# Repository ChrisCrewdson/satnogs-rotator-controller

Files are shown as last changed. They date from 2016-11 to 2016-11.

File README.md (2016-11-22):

# SatNOGS Rotator Controller

Firmware and electronics designs for [SatNOGS Rotator](https://github.com/satnogs/satnogs-rotator/).

Repository includes all source files for PCB's and firmware for the SatNOGS rotator controller assembly.

## Documentation

More information can be found in our [documentation](http://satnogs.org/documentation/hardware/), or our [wiki](https://wiki.satnogs.org).

Please check the documentation to find which release of the rotator controller matches your mechanical rotator version.

## Repository policy
SatNOGS hardware repositories only track source design files. All needed derivative files (e.g. stl, grb etc) for production are created per release, packaged in an archive and uploaded linked to a  [release](https://github.com/satnogs/satnogs-rotator-controller/releases).

Each major release (x.0.0) is branched out of master. Subsequent fixes (minor or not) are commited on those branches and tagged accordingly.

Master branch is most times under active development, so expect things to break. For production ready and previous releases source files check tags and branches.

## License

&copy; 2014-2015 [Libre Space Foundation](http://librespacefoundation.org).

Licensed under the [CERN OHLv1.2](LICENSE).

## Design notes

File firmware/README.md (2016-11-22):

Arduino Code
============

In order to use this code, you need to put the AccelStepper v1.46 library and SoftI2CMaster library in your libraries folder. Thanks to [AccelStepper library](http://www.airspayce.com/mikem/arduino/AccelStepper/) and [SoftI2CMaster](https://github.com/todbot/SoftI2CMaster).

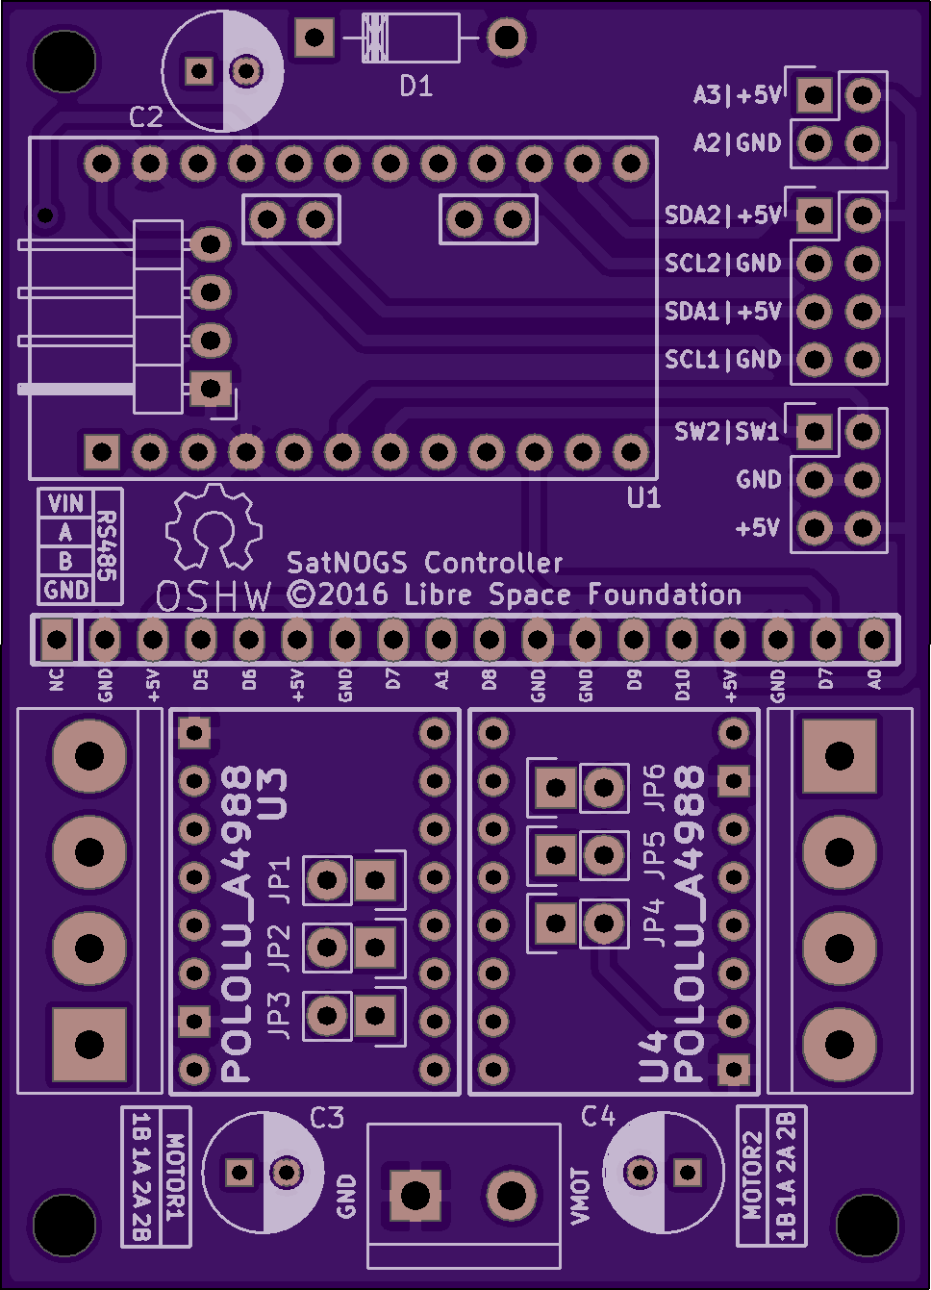
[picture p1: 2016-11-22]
PCB/satnogs_controller/oshpark_top.png

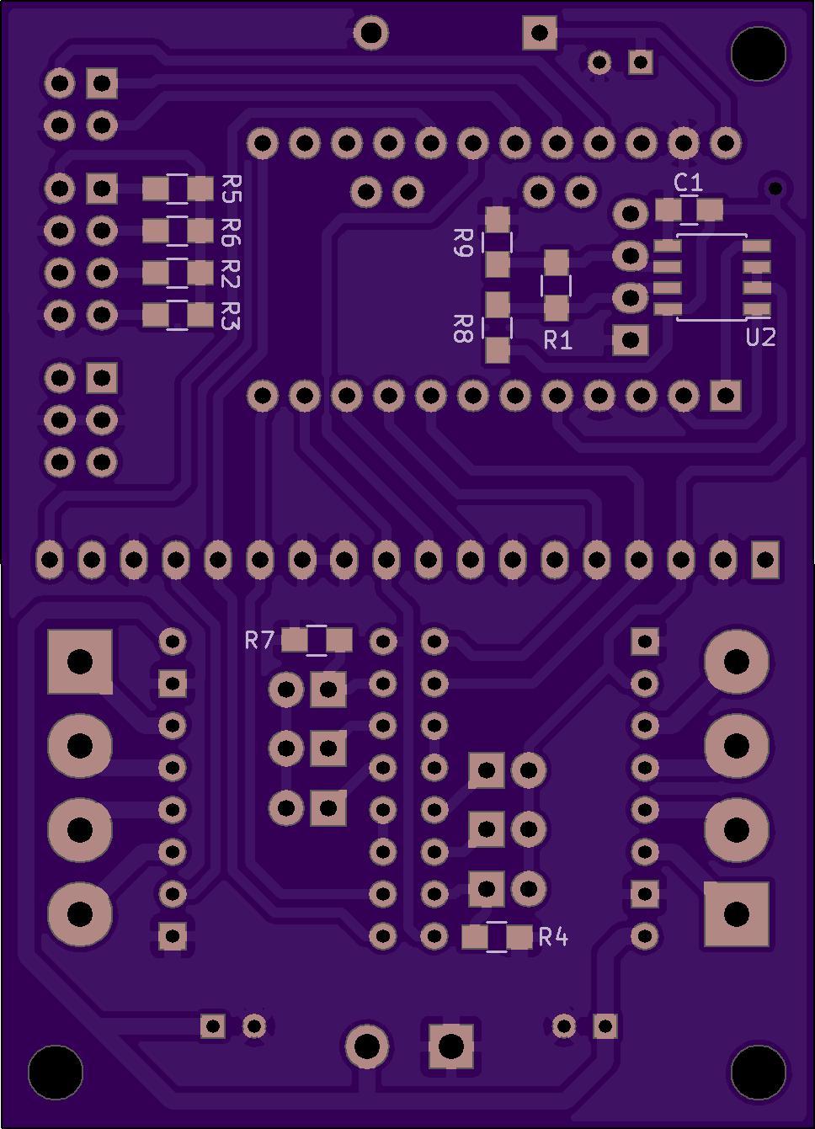
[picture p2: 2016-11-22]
PCB/satnogs_controller/oshpark_bottom.png

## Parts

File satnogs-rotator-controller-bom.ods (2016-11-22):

Part | Description | Distributor | Qty | Price Per Unit Small QNT (euro) | Total Price (euro) | Price Per Unit Large QNT (euro) | Total price | Comments
satnogs_controller, Parts | parts for satnogs_controller pcb | - | 1 | 15 | 15 | 0 | 0 | file: satnogs_controller.csv
satnogs_controller, PCB | pcb for satnogs_controller | [6] (https://oshpark.com/shared_projects/8eKNZnFG) | 1 | 8.5 | 8.5 | 0 | 0 | file: satnogs_controller.pro
Dual MC33926 Motor Driver Carrier | for DC Motors | [1] (https://www.pololu.com/product/1213) | 1 | 27 | 27 | 20.67 | 20.67 | DC Motor Driver
Pro Mini, Arduino | microcontroller | [2] (http://www.ebay.com/sch/i.html?_from=R40&_nkw=arduino+pro+mini&_sacat=0) | 1 | 2 | 2 | 0 | 0 | ATMega328p microcontroller,5V 16MHz, like this:http://www.arduino.cc/en/Main/ArduinoBoardProMini
USB to TTL and RS485 | Communication with Client | [4] (http://grobotronics.com/sparkfun-usb-to-rs-485-converter.html) | 1 | 10 | 10 | 10 | 10 | For long cable use RS485, otherwise TTL (ftdi cable)
A4988 Stepper Motor Driver Carrier | for Stepper Motors | [1] (https://www.pololu.com/product/1182) | 2 | 5.4 | 10.8 | 4.49 | 8.98 | Stepper Motor Driver
NEMA17 Stepper Motor | stepper Motors | [3] (http://www.omc-stepperonline.com/3d-printer-nema-17-stepper-motor-59ncm84ozin-2a-17hs192004s-p-18.html) | 2 | 10 | 20 | 0 | 0 | -
DC Motor | 50:1 Metal Gearmotor (37Dx54L) mm | [1] (https://www.pololu.com/product/1104) | 2 | 23 | 46 | 16.26 | 32.52 | -
Ceramic Capacitor 0.1uF | for DC Motors | [5] (http://gr.mouser.com/ProductDetail/Vishay-Sprague/1C20X7R104K050B/) | 4 | 0.15 | 0.6 | 0.1 | 0.4 | MLCC - Leaded 0.1uF 50volts X7R 10% 5.0mm L/S
satnogs_encoder, Parts | parts for satnogs_encoder pcb | - | 2 | 6 | 12 | 0 | 0 | file: encoder_as5601.csv
satnogs_encoder, PCB | pcb for satnogs_encoder | [6] (https://oshpark.com/shared_projects/s9OpwkRr) | 2 | 1.5 | 3 | 0 | 0 | file: encoder_as5601.pro
satnogs_endstop, Parts | parts for satnogs_endstop pcb | - | 2 | 5 | 10 | 0 | 0 | file: satnogs_endstop.csv
satnogs_endstop, PCB | pcb for satnogs_endstop | [6] (https://oshpark.com/shared_projects/z6IuY8sC) | 2 | 2 | 4 | 0 | 0 | file: satnogs_endstop.pro
switching adjustable step down voltage regulator | power supply | [2] (http://www.ebay.com/sch/i.html?_from=R40&_nkw=LM2596+DC+Switching+Adjustable&_sacat=0) | 1 | 2.5 | 2.5 | 0 | 0 | LM2596, VIN:3-40V, VOUT:1.5-35V, IMAX:3A
wire 0.25mm^2 (24AWG) | for signals and +5V,+3.3V | [4] (http://grobotronics.com/prototyping/hook-up-wires/) | 12 | 0.16 | 1.92 | 0 | 0 | black “-”, red “+”, purple “SDA1/2”, green “SCL1/2”, yellow “SW1”, blue “SW2”
wire 0.5mm^2 (20AWG) | for DC Motors | - | 4 | 0.25 | 1 | 0 | 0 | black “-”, red “+” (2m for both)
Terminal Female 2 Pins | for signals and +5V,+3.3V | [4] (http://grobotronics.com/terminal-female-2-pins-2.54mm-dupont.html) | 12 | 0.04 | 0.48 | 0 | 0 | Pitch 2.54mm
Terminal Female 1 Pins | for signals and +5V,+3.3V | [4] (http://grobotronics.com/terminal-female-1-pins-2.54mm.html) | 4 | 0.04 | 0.16 | 0 | 0 | Pitch 2.54mm
Crimp For Female Connectors | for signals and +5V,+3.3V | [4] (http://grobotronics.com/crimp-for-female-connectors-c-grid.html) | 28 | 0.04 | 1.12 | 0 | 0 | -
Aluminium Box | inside the rotator | [4] (http://grobotronics.com/project-box-120x100x35mm-aluminium.html) | 1 | 6.1 | 6.1 | 0 | 0 | (120x100x35)mm
Connector RJ45 for panel | for communication and power input | [5] (http://gr.mouser.com/ProductDetail/TE-Connectivity-AMP/216005-1/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) | 1 | 3.9 | 3.9 | 3.5 | 3.5 | Mount in Aluminium box
Diametric Magnet NdFeB, Grade N35, D6x2.5mm | for SatNOGS encoder | [4] (http://ams.com/eng/Products/Position-Sensors/Magnets/AS5000-MD6H-3) | 2 | 0.3 | 0.6 | 0.27 | 0.54 | [Other Shop] (https://www.magnet-shop.com/neodymium/discmagnets/discmagnet-4.0-x-4.0-mm-n35h-nickel-diametral-120c)
 |  |  |  | Total (DC Motors) | 155.88
*under research |  |  |  | Total (Stepper) | 113.68

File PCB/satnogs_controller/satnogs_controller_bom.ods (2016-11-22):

Reference | Value | Footprint | Notes | Datasheet | Manufacturer | Package
C1 | 0.1u | Capacitors_SMD:C_0805_HandSoldering | 0805 | http://www.mouser.com/ds/2/427/vjw1bcbascomseries-223529.pdf | Mouser 77-VJ0805Y104KXJCBC | VJ0805Y104KXJCW1BC | https://www.sparkfun.com/products/115
C2 | 10u | Capacitors_ThroughHole:C_Radial_D6.3_L11.2_P2.5 | ThroughHole:C_Radial_D6.3_L11.2_P2.5 | http://www.mouser.com/ds/2/315/ABA0000CE12-465472.pdf | Mouser 667-ECA-1EM100B | ECA-1EM100B | https://www.sparkfun.com/products/553
C3 | 100u | Capacitors_ThroughHole:C_Radial_D6.3_L11.2_P2.5 | ThroughHole:C_Radial_D6.3_L11.2_P2.5 | http://www.mouser.com/ds/2/315/ABA0000CE12-465472.pdf | Mouser 667-ECA-1VM101 | ECA-1VM101 | https://www.sparkfun.com/products/12791
C4 | 100u | Capacitors_ThroughHole:C_Radial_D6.3_L11.2_P2.5 | ThroughHole:C_Radial_D6.3_L11.2_P2.5 | http://www.mouser.com/ds/2/315/ABA0000CE12-465472.pdf | Mouser 667-ECA-1VM101 | ECA-1VM101 | 16VDC
D1 | ZENERsmall | Diodes_ThroughHole:Diode_DO-41_SOD81_Horizontal_RM10 | DO-41 | http://www.mouser.com/ds/2/149/BZX85C10-888846.pdf | Mouser 512-BZX85C10 | BZX85C10 | 10uF 25VDC 85C
JP1 | Jumper_NO_Small | Pin_Headers:Pin_Header_Straight_1x02 | 2x23 pin male PTH header | https://cdn.sparkfun.com/datasheets/Prototyping/16188.pdf | SparkFun PRT-12791 | - | https://www.sparkfun.com/products/12791
JP2 | Jumper_NO_Small | Pin_Headers:Pin_Header_Straight_1x02 | 2x23 pin male PTH header | https://cdn.sparkfun.com/datasheets/Prototyping/16188.pdf | SparkFun PRT-12791 | - | Operating Supply Voltage: 5 V
JP3 | Jumper_NO_Small | Pin_Headers:Pin_Header_Straight_1x02 | 2x23 pin male PTH header | https://cdn.sparkfun.com/datasheets/Prototyping/16188.pdf | SparkFun PRT-12791 | - | https://www.sparkfun.com/products/115
JP4 | Jumper_NO_Small | Pin_Headers:Pin_Header_Straight_1x02 | 2x23 pin male PTH header | https://cdn.sparkfun.com/datasheets/Prototyping/16188.pdf | SparkFun PRT-12791 | - | 100u 35V 85C
JP5 | Jumper_NO_Small | Pin_Headers:Pin_Header_Straight_1x02 | 2x23 pin male PTH header | https://cdn.sparkfun.com/datasheets/Prototyping/16188.pdf | SparkFun PRT-12791 | - | https://www.sparkfun.com/products/12791
JP6 | Jumper_NO_Small | Pin_Headers:Pin_Header_Straight_1x02 | 2x23 pin male PTH header | https://cdn.sparkfun.com/datasheets/Prototyping/16188.pdf | SparkFun PRT-12791 | - | https://www.sparkfun.com/products/12791
P1 | RS485 | Pin_Headers:Pin_Header_Angled_1x04 | 1x40 pin right-angle PTH pitch 2.54 | - | SparkFun PRT-00553 | - | https://www.sparkfun.com/products/12791
P2 | End-Stops | Pin_Headers:Pin_Header_Straight_2x03 | 2x23 pin male PTH header | https://cdn.sparkfun.com/datasheets/Prototyping/16188.pdf | SparkFun PRT-12791 | - | 1/8W 5%
P4 | I2C | Pin_Headers:Pin_Header_Straight_2x04 | 2x23 pin male PTH header | https://cdn.sparkfun.com/datasheets/Prototyping/16188.pdf | SparkFun PRT-12791 | - | https://www.sparkfun.com/products/8432
P5 | DC Motors Driver | satnogs:pin_socket_18 | 1x40 female header PTH pitch 2.54 | - | SparkFun PRT-00115 | - | https://www.sparkfun.com/products/115
P6 | Power-IN | Connect:bornier2 | 5mm Pitch | https://www.sparkfun.com/datasheets/Prototyping/Screw-Terminal-5mm.pdf | SparkFun PRT-08432 | - | 100u 35V 85C
P7 | Motor1 | Connect:bornier4 | 5mm Pitch 4-Pin | https://www.sparkfun.com/datasheets/Prototyping/Screw-Terminal-5mm.pdf | SparkFun PRT-08432 | - | https://www.sparkfun.com/products/12791
P8 | Motor2 | Connect:bornier4 | 5mm Pitch 4-Pin | https://www.sparkfun.com/datasheets/Prototyping/Screw-Terminal-5mm.pdf | SparkFun PRT-08432 | - | https://www.sparkfun.com/products/12791
P9 | Dev-Pins | Pin_Headers:Pin_Header_Straight_2x02 | - | https://cdn.sparkfun.com/datasheets/Prototyping/16188.pdf | SparkFun PRT-12791 | - | https://www.sparkfun.com/products/12791
R1 | 120 | Resistors_SMD:R_0805_HandSoldering | 0805 | http://www.mouser.com/ds/2/427/dcrcwe3-109170.pdf | Mouser 71-CRCW0805120RJNEA | CRCW0805120RJNEA | 1/8W 5%
R2 | 4.7k | Resistors_SMD:R_0805_HandSoldering | 0805 | http://www.mouser.com/ds/2/427/dcrcwe3-109170.pdf | Mouser 71-CRCW0805J-4.7K-E3 | CRCW08054K70JNEA | https://www.sparkfun.com/products/8432
R3 | 4.7k | Resistors_SMD:R_0805_HandSoldering | 0805 | http://www.mouser.com/ds/2/427/dcrcwe3-109170.pdf | Mouser 71-CRCW0805J-4.7K-E3 | CRCW08054K70JNEA | https://www.sparkfun.com/products/8432
R4 | 100k | Resistors_SMD:R_0805_HandSoldering | 0805 | http://www.mouser.com/ds/2/427/dcrcwe3-109170.pdf | Mouser 71-CRCW0805J-100K-E3 | CRCW0805100KJNEA | 1/8W 5%
R5 | 4.7k | Resistors_SMD:R_0805_HandSoldering | 0805 | http://www.mouser.com/ds/2/427/dcrcwe3-109170.pdf | Mouser 71-CRCW0805J-4.7K-E3 | CRCW08054K70JNEA | 1/8W 5%
R6 | 4.7k | Resistors_SMD:R_0805_HandSoldering | 0805 | http://www.mouser.com/ds/2/427/dcrcwe3-109170.pdf | Mouser 71-CRCW0805J-4.7K-E3 | CRCW08054K70JNEA | 1/8W 5%
R7 | 100k | Resistors_SMD:R_0805_HandSoldering | 0805 | http://www.mouser.com/ds/2/427/dcrcwe3-109170.pdf | Mouser 71-CRCW0805J-100K-E3 | CRCW0805100KJNEA | 1/8W 5%
R8 | 4.7k | Resistors_SMD:R_0805_HandSoldering | 0805 | http://www.mouser.com/ds/2/427/dcrcwe3-109170.pdf | Mouser 71-CRCW0805J-4.7K-E3 | CRCW08054K70JNEA | 1/8W 5%
R9 | 4.7k | Resistors_SMD:R_0805_HandSoldering | 0805 | http://www.mouser.com/ds/2/427/dcrcwe3-109170.pdf | Mouser 71-CRCW0805J-4.7K-E3 | CRCW08054K70JNEA | 1/8W 5%
U1 | Pro_Mini | satnogs:pro-mini | 1x40 female header PTH pitch 2.54 | - | SparkFun PRT-00115 | - | 1/8W 5%
U2 | MAX485 | Housings_SOIC:SOIC-8_3.9x4.9mm_Pitch1.27mm | SOIC-8 Narrow | http://www.mouser.com/ds/2/146/SP483_SP485_100_062711-16528.pdf | Mouser 701-SP485CN-L | SP485CN-L | https://www.sparkfun.com/products/115
U3 | POLOLU_A4988 | satnogs:SWDIP8_.6W | 1x40 female header PTH pitch 2.54 | - | SparkFun PRT-00115 | - | 10V-1W
U4 | POLOLU_A4988 | satnogs:SWDIP8_.6W | 1x40 female header PTH pitch 2.54 | - | SparkFun PRT-00115 | - | https://www.sparkfun.com/products/12791

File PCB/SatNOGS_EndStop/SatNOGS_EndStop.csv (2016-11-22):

Reference | Value | Footprint | Datasheet | Distributor | Manufacturer | Package | Notes | Price
SW1 | TCST2103 | satnogs:TCST2103 | http://www.mouser.com/ds/2/427/tcst2103-279826.pdf |  | Mouser 782-TCST2103 | TCST2103 | - | - | 1.59€
R1 | 180 | Resistors_SMD:R_0805_HandSoldering | http://www.mouser.com/ds/2/427/dcrcwe3-109170.pdf |  | Mouser 71-CRCW0805180RJNEA | CRCW0805180RJNEA | 0805 | 1/8W 5% | 0.091 €
R2 | 1k5 | Resistors_SMD:R_0805_HandSoldering | http://www.mouser.com/ds/2/427/dcrcwe3-109170.pdf |  | Mouser 71-CRCW0805J-1.5K-E3 | CRCW08051K50JNEA | 0805 | 1/8W 5% | 0.091€
R3 | 1k | Resistors_SMD:R_0805_HandSoldering | http://www.mouser.com/ds/2/427/dcrcwe3-109170.pdf |  | Mouser 71-CRCW08051K00JNEB | CRCW08051K00JNEB | 0805 | 1/8W 5% | 0.091€
D1 | LED | LEDs:LED-3MM | https://www.sparkfun.com/datasheets/Components/LED/YSL-R341K3D-D2.pdf |  | SparkFun COM-09650 | - | Green 3mm pitch 2.54 | - | 0.33€
P1 | CONN_01X03 | Pin_Headers:Pin_Header_Angled_1x03 | - |  | SparkFun PRT-00553 | - | 1x40 pin right-angle pitch 2.54 | - | 1.85€
Q1 | Q_NMOS_GSD | TO_SOT_Packages_SMD:SOT-23_Handsoldering | http://www.mouser.com/ds/2/427/SI2312CD-244454.pdf |  | Mouser 781-SI2312CDS-T1-GE3 | SI2312CDS-T1-GE3 | SOT-23-3 | - | 0.398

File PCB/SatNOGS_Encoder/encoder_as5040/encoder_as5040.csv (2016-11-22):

Reference | Value | Footprint | Datasheet | Distributor | Manufacturer | Package | Notes | Price
U1 | AS5040 | Housings_SSOP:SSOP-16_5.3x6.2mm_Pitch0.65mm | http://www.mouser.com/ds/2/588/AS5040_Datasheet_EN_v2-473299.pdf | Mouser 985-AS5040-ASST | AS5040-ASST | SSOP-16 | - | 8.73 €
R2 | 560 | Resistors_SMD:R_0805_HandSoldering | http://www.mouser.com/ds/2/427/dcrcwe3-109170.pdf | Mouser 71-CRCW0805560RJNEA | CRCW0805560RJNEA | 805 | 1/8W 5% | 0.091€
R1 | 560 | Resistors_SMD:R_0805_HandSoldering | http://www.mouser.com/ds/2/427/dcrcwe3-109170.pdf | Mouser 71-CRCW0805560RJNEA | CRCW0805560RJNEA | 805 | 1/8W 5% | 0.091€
R3 | 100 | Resistors_SMD:R_0805_HandSoldering | http://www.mouser.com/ds/2/427/dcrcwe3-109170.pdf | Mouser 71-CRCW0805J-100-E3 | CRCW0805100RJNEC | 805 | 1/8W 5% | 0.091€
C1 | 1n | Capacitors_SMD:C_0805_HandSoldering | http://www.mouser.com/ds/2/427/vjw1bcbascomseries-223529.pdf | Mouser 77-VJ0805A102KXJPBC | VJ0805A102KXJPW1BC | 805 | 16VDC | 0.091€
C4 | 100n | Capacitors_SMD:C_0805_HandSoldering | http://www.mouser.com/ds/2/427/vjw1bcbascomseries-223529.pdf | Mouser 77-VJ0805Y104KXJCBC | VJ0805Y104KXJCW1BC | 805 | 16VDC | 0.118€
C2 | 1u | Capacitors_SMD:C_0805_HandSoldering | http://www.mouser.com/ds/2/427/vjw1bcbascomseries-223529.pdf | Mouser 77-VJ0805V105ZXJCBC | VJ0805V105ZXJCW1BC | 805 | 16VDC | 0.091€
C3 | 1u | Capacitors_SMD:C_0805_HandSoldering | http://www.mouser.com/ds/2/427/vjw1bcbascomseries-223529.pdf | Mouser 77-VJ0805V105ZXJCBC | VJ0805V105ZXJCW1BC | 805 | 16VDC | 0.091€
P1 | CONN_02X07 | Pin_Headers:Pin_Header_Straight_2x07 | https://cdn.sparkfun.com/datasheets/Prototyping/01103.pdf | SparkFun COM-12792 | - | 2x40 pin right-angle PTH pitch 2.54 | - | 1.85€
D1 | LED | LEDs:LED-3MM | https://www.sparkfun.com/datasheets/Components/LED/YSL-R341K3D-D2.pdf | SparkFun COM-09650 | - | Green 3mm pitch 2.54 | - | 0.33€
D2 | LED | LEDs:LED-3MM | https://www.sparkfun.com/datasheets/Components/LED/YSL-R341K3D-D2.pdf | SparkFun COM-09650 | - | Green 3mm pitch 2.54 | - | 0.33€

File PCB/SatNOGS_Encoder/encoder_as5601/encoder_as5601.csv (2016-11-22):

Reference | Value | Footprint | Datasheet | Distributor | Manufacturer | Package | Notes | Price
U1 | AS5601 | Housings_SOIC:SOIC-8_3.9x4.9mm_Pitch1.27mm | www.mouser.com/ds/2/588/AS5601_Datasheet-771178.pdf |  | Mouser 985-AS5601-ASOM | AS5601-ASOM | SOIC-8 | - | 2.78€
C1 | 100n | Capacitors_SMD:C_0805_HandSoldering | - |  | - | - | 0805 | - | 0.1€
C2 | 1u | Capacitors_SMD:C_0805_HandSoldering | - |  | - | - | 0805 | - | 0.1 €
P1 | CONN_02X05 | Pin_Headers:Pin_Header_Straight_2x05 | https://cdn.sparkfun.com/datasheets/Prototyping/01103.pdf |  | SparkFun COM-12792 | - | 2x40 pin right-angle PTH pitch 2.54 | - | 1.85€
R1 | 4k7 | Resistors_SMD:R_0805_HandSoldering | - |  | - | - | 0805 | - | 0.1 €
R2 | 4k7 | Resistors_SMD:R_0805_HandSoldering | - |  | - | - | 0805 | - | 0.1 €
Q1 | Q_NMOS_GSD | TO_SOT_Packages_SMD:SOT-23_Handsoldering | http://www.mouser.com/ds/2/427/SI2312CD-244454.pdf |  | Mouser 781-SI2312CDS-T1-GE3 | SI2312CDS-T1-GE3 | SOT-23-3 | - | 0.398

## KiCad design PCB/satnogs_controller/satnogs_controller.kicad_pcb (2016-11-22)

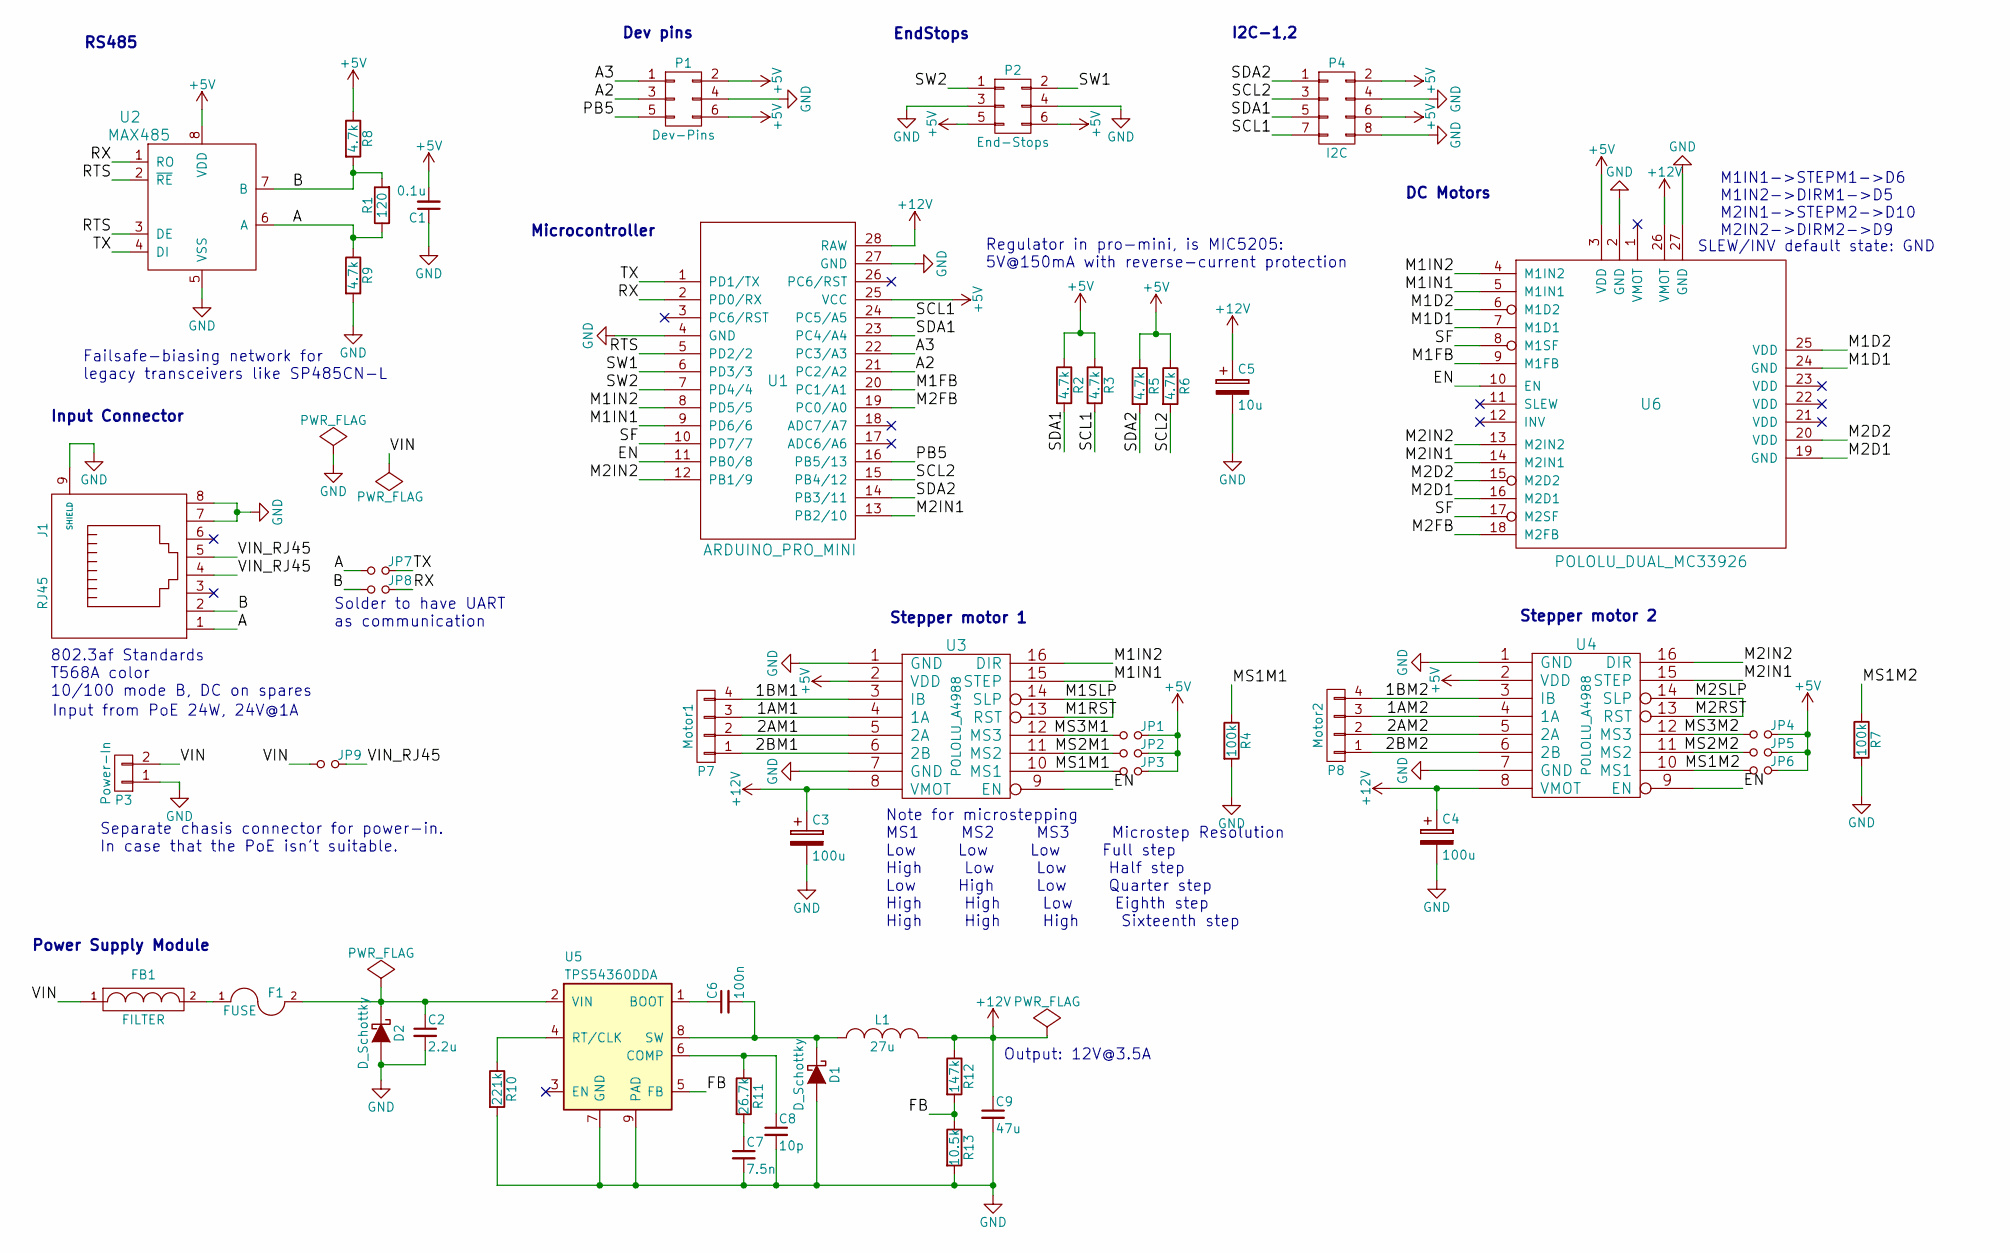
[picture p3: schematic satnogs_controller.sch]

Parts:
C1: 0.1u; C_0805_HandSoldering
C2: 2.2u; C_1210
C3, C4: 100u; C_Radial_D6.3_L11.2_P2.5
C5: 10u; C_Radial_D6.3_L11.2_P2.5
C6: 100n; C_0805_HandSoldering
C7: 7.5n; C_0805_HandSoldering
C8: 10p; C_0805_HandSoldering
C9: 47u; C_1210
D1, D2: D_Schottky; DO-214AB
F1: FUSE; Fuse_SMD
FB1: FILTER; R_0805_HandSoldering
J1: RJ45; RJ45_8
JP1, JP2, JP3, JP4, JP5, JP6, JP7, JP8, JP9: Jumper_NO_Small; R_0805_HandSoldering
L1: 27u; bourns-srr1210
P1: Dev-Pins; Pin_Header_Straight_2x03
P2: End-Stops; Pin_Header_Straight_2x03
P3: Power-In; WireConnection_2.00mmDrill
P4: I2C; Pin_Header_Straight_2x04
P7: Motor1; bornier4
P8: Motor2; bornier4
R1: 120; R_0805_HandSoldering
R2, R3, R5, R6, R8, R9: 4.7k; R_0805_HandSoldering
R4, R7: 100k; R_0805_HandSoldering
R10: 221k; R_0805_HandSoldering
R11: 26.7k; R_0805_HandSoldering
R12: 147k; R_0805_HandSoldering
R13: 10.5k; R_0805_HandSoldering
U1: ARDUINO_PRO_MINI; arduino-pro-mini
U2: MAX485; SOIC-8_3.9x4.9mm_Pitch1.27mm
U3, U4: POLOLU_A4988; pololu-a4988
U5: TPS54360DDA; HSOP-8
U6: POLOLU_DUAL_MC33926; pololu-dual-mc33926

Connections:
+5V: C1.2, JP1.2, JP2.2, JP3.2, JP4.2, JP5.2, JP6.2, P1.2, P1.6, P2.5, P2.6, P4.2, P4.6, R2.1, R3.1, R5.1, R6.1, R8.1, U1.25 (VCC), U2.8 (VDD), U3.2 (VDD), U4.2 (VDD), U6.3 (VDD)
+12V: C3.1, C4.1, C5.1, C9.1, L1.2, R12.1, U1.28 (RAW), U3.8 (VMOT), U4.8 (VMOT), U6.26 (VMOT)
/1AM1: P7.3, U3.4 (1A)
/1AM2: P8.3, U4.4 (1A)
/1BM1: P7.4, U3.3 (IB)
/1BM2: P8.4, U4.3 (IB)
/2AM1: P7.2, U3.5 (2A)
/2AM2: P8.2, U4.5 (2A)
/2BM1: P7.1, U3.6 (2B)
/2BM2: P8.1, U4.6 (2B)
/A: J1.1, JP7.1, R1.1, R9.1, U2.6 (A)
/A2: P1.3, U1.21 (PC2/A2)
/A3: P1.1, U1.22 (PC3/A3)
/B: J1.2, JP8.1, R1.2, R8.2, U2.7 (B)
/EN: U1.11 (PB0/8), U3.9 (EN), U4.9 (EN), U6.10 (EN)
/FB: R12.2, R13.1, U5.5 (FB)
/M1D1: U6.7 (M1D1), U6.24 (GND)
/M1D2: U6.6 (M1D2), U6.25 (VDD)
/M1FB: U1.20 (PC1/A1), U6.9 (M1FB)
/M1IN1: U1.9 (PD6/6), U3.15 (STEP), U6.5 (M1IN1)
/M1IN2: U1.8 (PD5/5), U3.16 (DIR), U6.4 (M1IN2)
/M1RST: U3.13 (RST), U3.14 (SLP)
/M2D1: U6.16 (M2D1), U6.19 (GND)
/M2D2: U6.15 (M2D2), U6.20 (VDD)
/M2FB: U1.19 (PC0/A0), U6.18 (M2FB)
/M2IN1: U1.13 (PB2/10), U4.15 (STEP), U6.14 (M2IN1)
/M2IN2: U1.12 (PB1/9), U4.16 (DIR), U6.13 (M2IN2)
/M2RST: U4.13 (RST), U4.14 (SLP)
/MS1M1: JP3.1, R4.1, U3.10 (MS1)
/MS1M2: JP6.1, R7.1, U4.10 (MS1)
/MS2M1: JP2.1, U3.11 (MS2)
/MS2M2: JP5.1, U4.11 (MS2)
/MS3M1: JP1.1, U3.12 (MS3)
/MS3M2: JP4.1, U4.12 (MS3)
/PB5: P1.5, U1.16 (PB5/13)
/RTS: U1.5 (PD2/2), U2.2 (~RE), U2.3 (DE)
/RX: JP8.2, U1.2 (PD0/RX), U2.1 (RO)
/SCL1: P4.7, R3.2, U1.24 (PC5/A5)
/SCL2: P4.3, R6.2, U1.15 (PB4/12)
/SDA1: P4.5, R2.2, U1.23 (PC4/A4)
/SDA2: P4.1, R5.2, U1.14 (PB3/11)
/SF: U1.10 (PD7/7), U6.8 (M1SF), U6.17 (M2SF)
/SW1: P2.2, U1.6 (PD3/3)
/SW2: P2.1, U1.7 (PD4/4)
/TX: JP7.2, U1.1 (PD1/TX), U2.4 (DI)
/VIN: FB1.1, JP9.1, P3.2
/VIN_RJ45: J1.4, J1.5, JP9.2
GND: C1.1, C2.2, C3.2, C4.2, C5.2, C7.2, C8.2, C9.2, D1.2 (A), D2.2 (A), J1.7, J1.8, J1.9 (SHIELD), P1.4, P2.3, P2.4, P3.1, P4.4, P4.8, R4.2, R7.2, R9.2, R10.2, R13.2, U1.4 (GND), U1.27 (GND), U2.5 (VSS), U3.1 (GND), U3.7 (GND), U4.1 (GND), U4.7 (GND), U5.7 (GND), U5.9 (PAD), U6.2 (GND), U6.27 (GND)
unnamed: C2.1, D2.1 (K), F1.2, U5.2 (VIN)
unnamed: C6.1, U5.1 (BOOT)
unnamed: C6.2, D1.1 (K), L1.1, U5.8 (SW)
unnamed: C7.1, R11.2
unnamed: C8.1, R11.1, U5.6 (COMP)
unnamed: F1.1, FB1.2
unnamed: R10.1, U5.4 (RT/CLK)

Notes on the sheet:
M1IN1->STEPM1->D6 M1IN2->DIRM1->D5 M2IN1->STEPM2->D10 M2IN2->DIRM2->D9
I2C-1,2
EndStops
DC Motors
Microcontroller
RS485
Stepper motor 1
Stepper motor 2
Dev pins
Regulator in pro-mini, is MIC5205: 5V@150mA with reverse-current protection
Failsafe-biasing network for legacy transceivers like SP485CN-L
Input Connector
Note for microstepping MS1 MS2 MS3 Microstep Resolution Low Low Low Full step High Low Low Half step Low High Low Quarter step High High Low Eighth step High High High Sixteenth step
802.3af Standards T568A color 10/100 mode B, DC on spares
Input from PoE 24W, 24V@1A
SLEW/INV default state: GND
Power Supply Module
Solder to have UART as communication
Output: 12V@3.5A
Separate chasis connector for power-in. In case that the PoE isn't suitable.

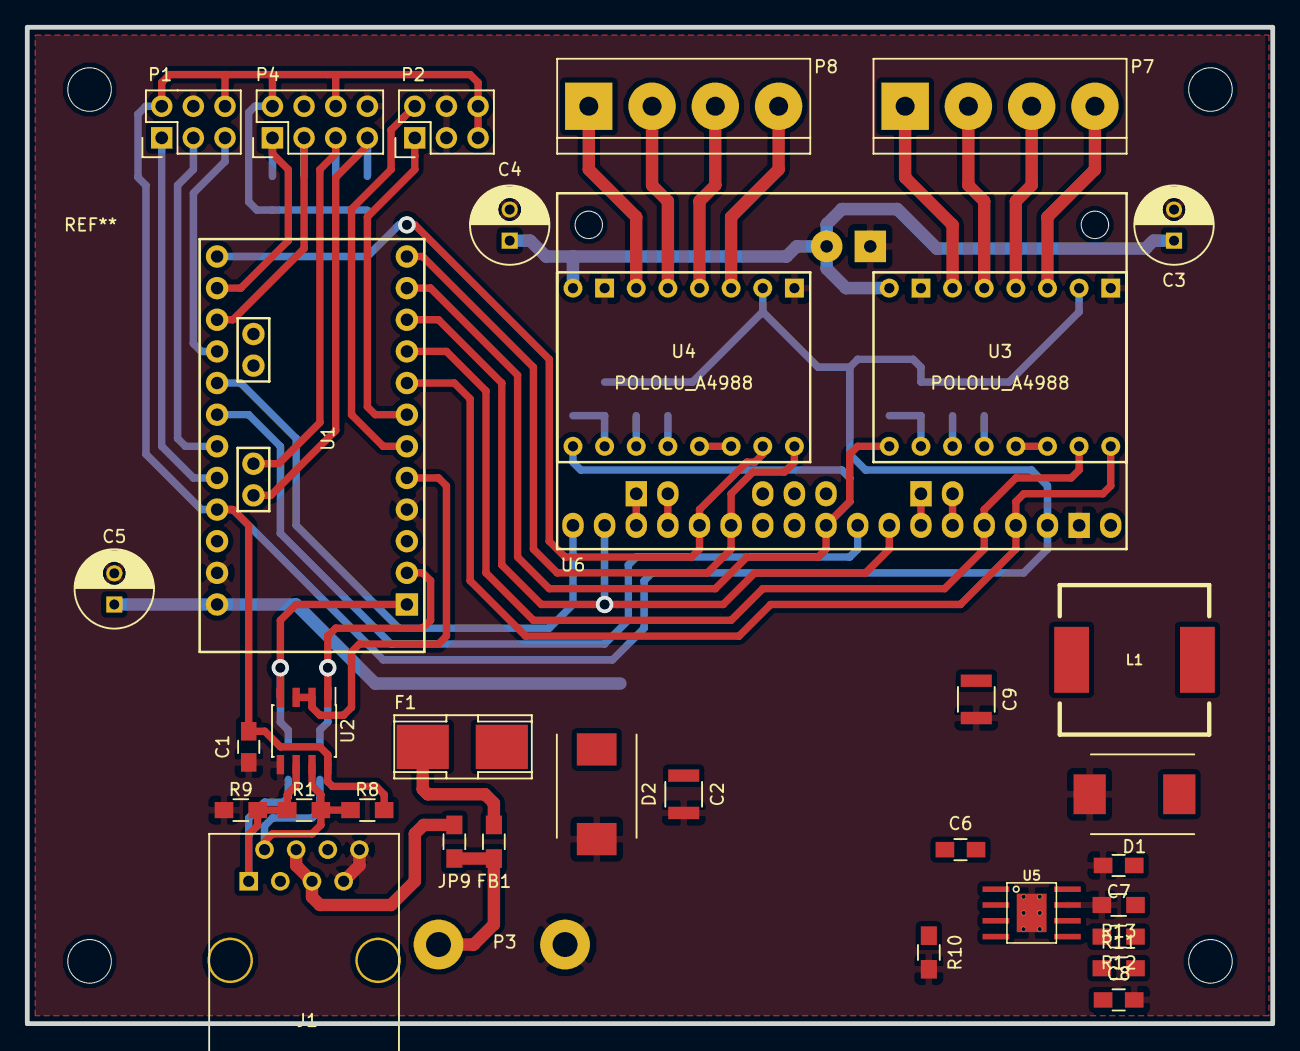
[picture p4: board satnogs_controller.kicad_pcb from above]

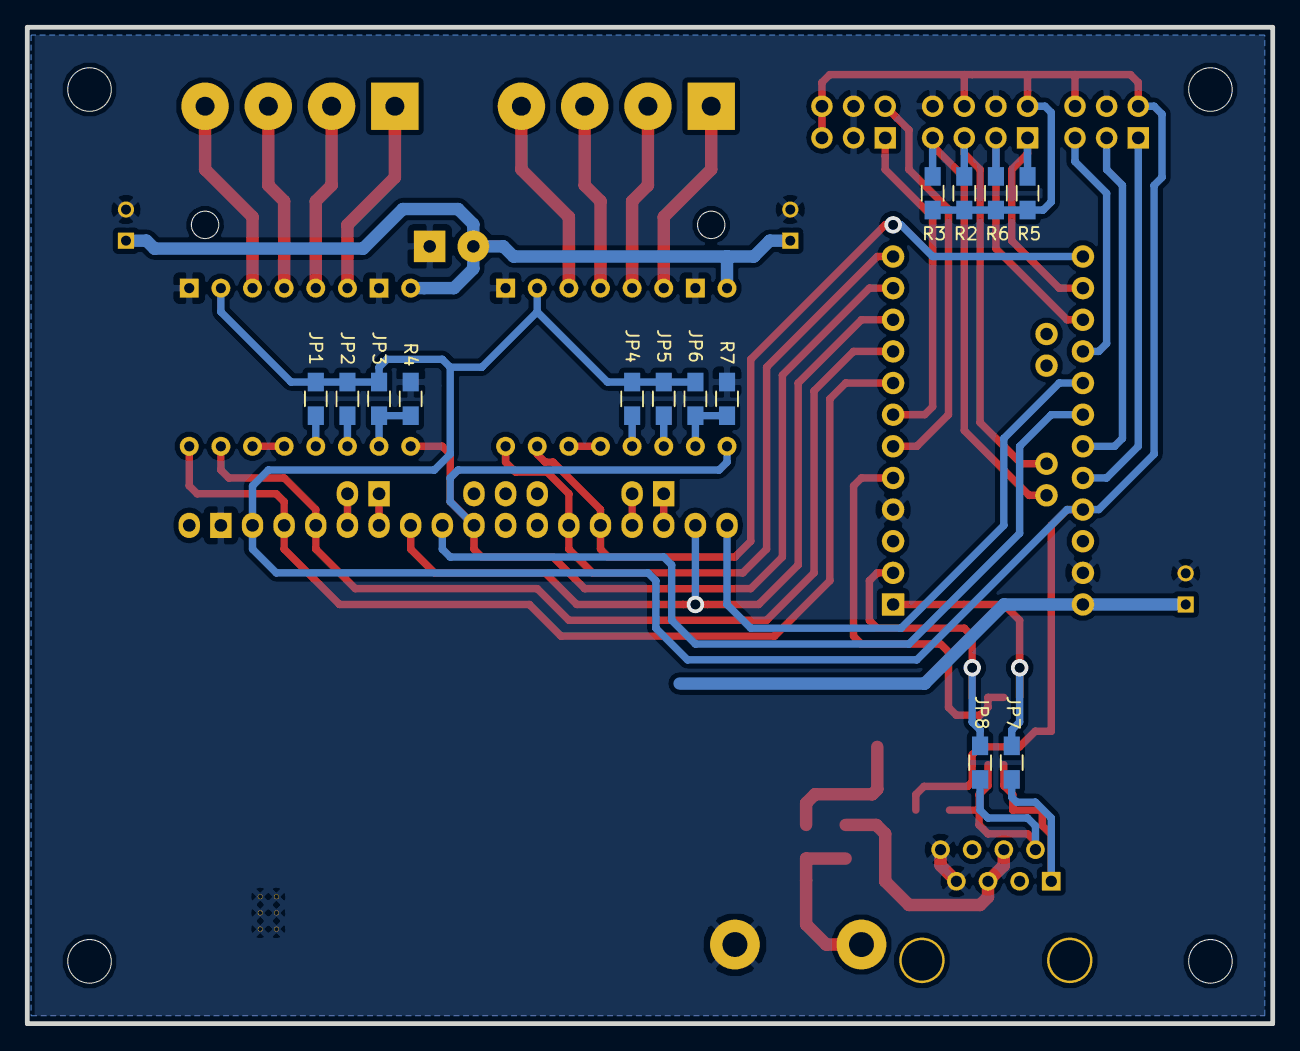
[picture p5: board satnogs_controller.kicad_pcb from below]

Board: 2 copper layers, 100.0 x 80.0 mm, 49 parts (14 on the bottom side), 55 nets.

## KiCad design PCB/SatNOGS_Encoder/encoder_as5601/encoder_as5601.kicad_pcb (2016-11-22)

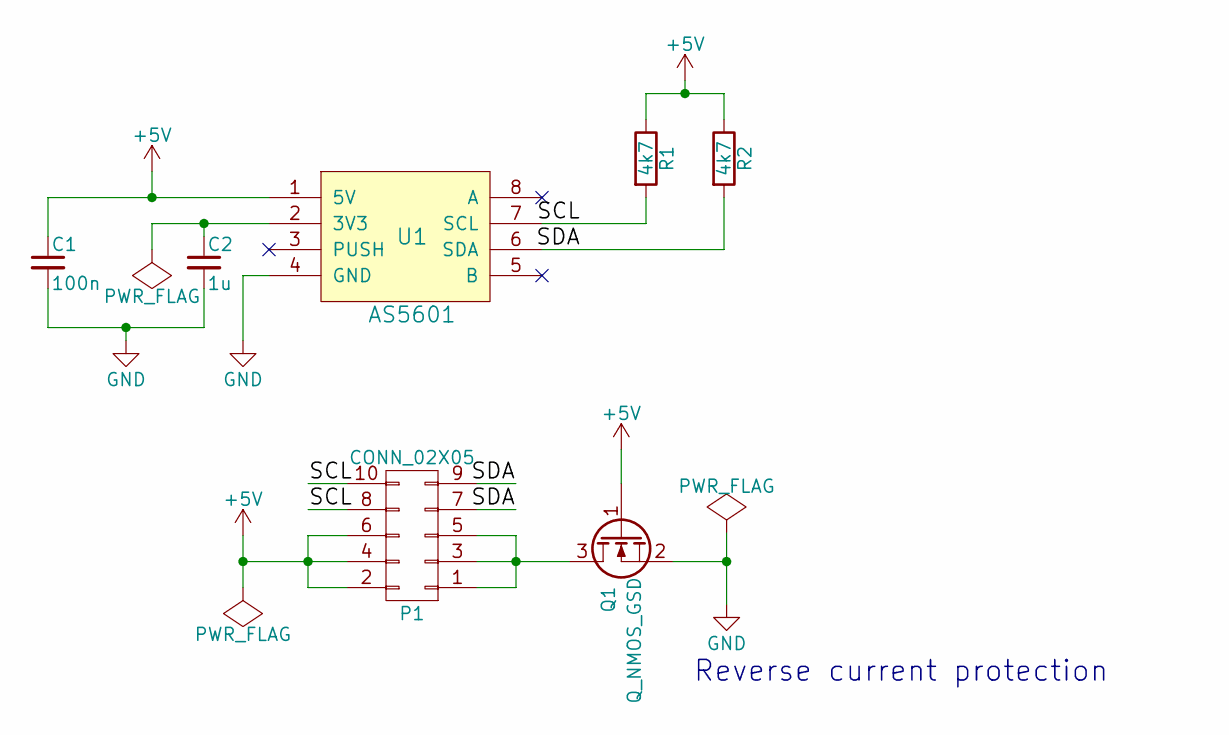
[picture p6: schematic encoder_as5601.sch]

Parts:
C1: 100n; C_0805_HandSoldering
C2: 1u; C_0805_HandSoldering
P1: CONN_02X05; Pin_Header_Straight_2x05
Q1: Q_NMOS_GSD; SOT-23_Handsoldering
R1, R2: 4k7; R_0805_HandSoldering
U1: AS5601; SOIC-8_3.9x4.9mm_Pitch1.27mm

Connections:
+5V: C1.1, P1.2, P1.4, P1.6, Q1.1 (G), R1.1, R2.1, U1.1 (5V)
/SCL: P1.8, P1.10, R1.2, U1.7 (SCL)
/SDA: P1.7, P1.9, R2.2, U1.6 (SDA)
GND: C1.2, C2.2, Q1.2 (S), U1.4 (GND)
unnamed: C2.1, U1.2 (3V3)
unnamed: P1.1, P1.3, P1.5, Q1.3 (D)

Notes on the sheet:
Reverse current protection

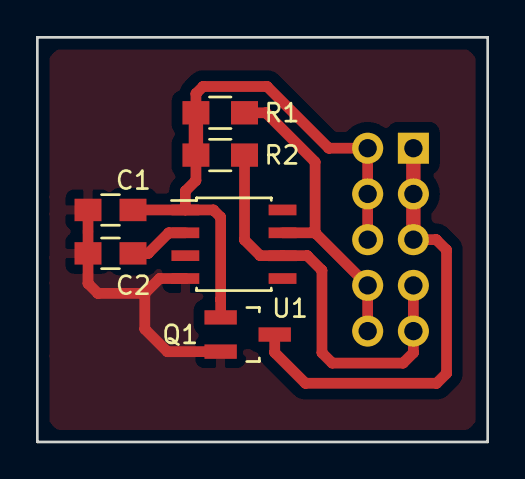
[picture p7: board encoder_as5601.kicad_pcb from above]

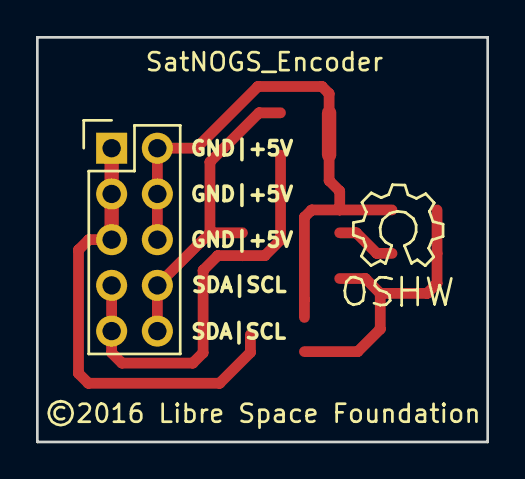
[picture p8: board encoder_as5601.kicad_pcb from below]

Board: 2 copper layers, 25.0 x 22.5 mm, 8 parts (2 on the bottom side), 6 nets.

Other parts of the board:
SatNOGS_Encoder: ©2016 Libre Space Foundation; Symbol_OSHW-Logo_SilkScreen

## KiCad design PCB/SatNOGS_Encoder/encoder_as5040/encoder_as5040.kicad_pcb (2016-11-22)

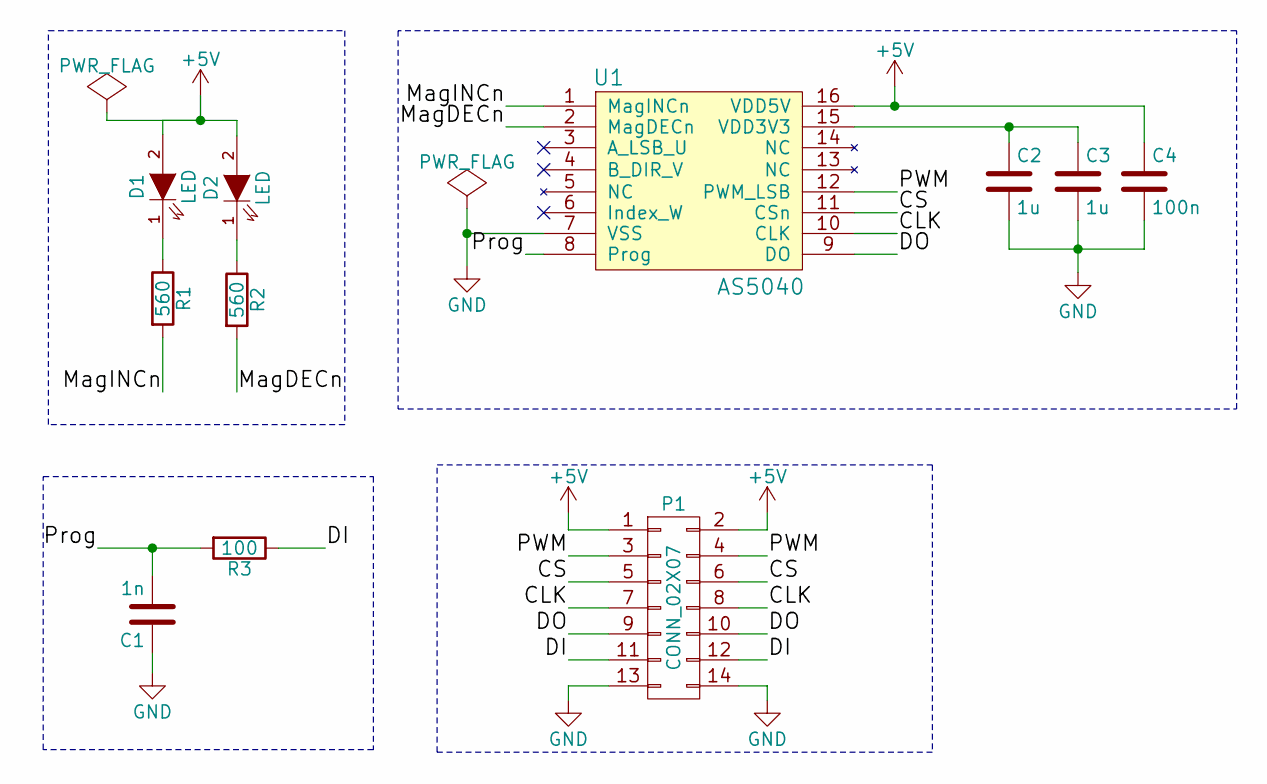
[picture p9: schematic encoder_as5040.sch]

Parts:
C1: 1n; C_0805_HandSoldering
C2, C3: 1u; C_0805_HandSoldering
C4: 100n; C_0805_HandSoldering
D1, D2: LED; LED-3MM
P1: CONN_02X07; Pin_Header_Straight_2x07
R1, R2: 560; R_0805_HandSoldering
R3: 100; R_0805_HandSoldering
U1: AS5040; SSOP-16_5.3x6.2mm_Pitch0.65mm

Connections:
+5V: C4.1, D1.2 (A), D2.2 (A), P1.1, P1.2, U1.16 (VDD5V)
/CLK: P1.7, P1.8, U1.10 (CLK)
/CS: P1.5, P1.6, U1.11 (CSn)
/DI: P1.11, P1.12, R3.1
/DO: P1.9, P1.10, U1.9 (DO)
/MagDECn: R2.2, U1.2 (MagDECn)
/MagINCn: R1.2, U1.1 (MagINCn)
/PWM: P1.3, P1.4, U1.12 (PWM_LSB)
/Prog: C1.2, R3.2, U1.8 (Prog)
GND: C1.1, C2.2, C3.2, C4.2, P1.13, P1.14, U1.7 (VSS)
unnamed: C2.1, C3.1, U1.15 (VDD3V3)
unnamed: D1.1 (K), R1.1
unnamed: D2.1 (K), R2.1

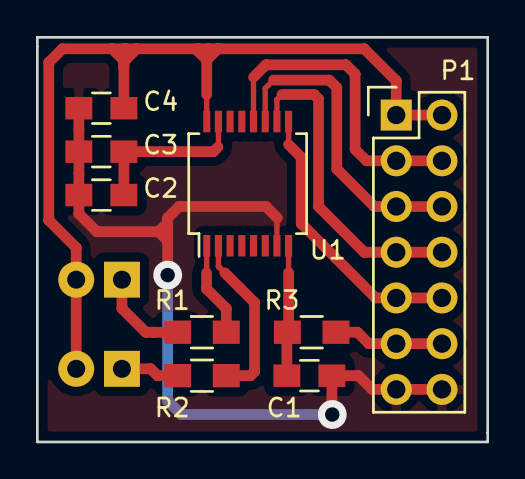
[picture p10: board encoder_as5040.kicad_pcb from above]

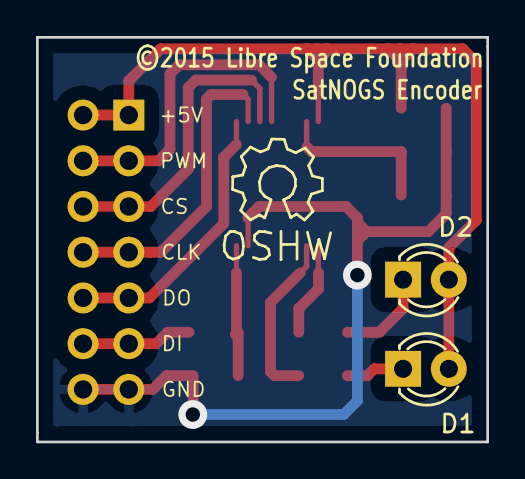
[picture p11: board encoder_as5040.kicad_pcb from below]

Board: 2 copper layers, 25.0 x 22.5 mm, 12 parts (3 on the bottom side), 13 nets.

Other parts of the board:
©2015 Libre Space Foundation: SatNOGS Encoder; Symbol_OSHW-Logo_SilkScreen

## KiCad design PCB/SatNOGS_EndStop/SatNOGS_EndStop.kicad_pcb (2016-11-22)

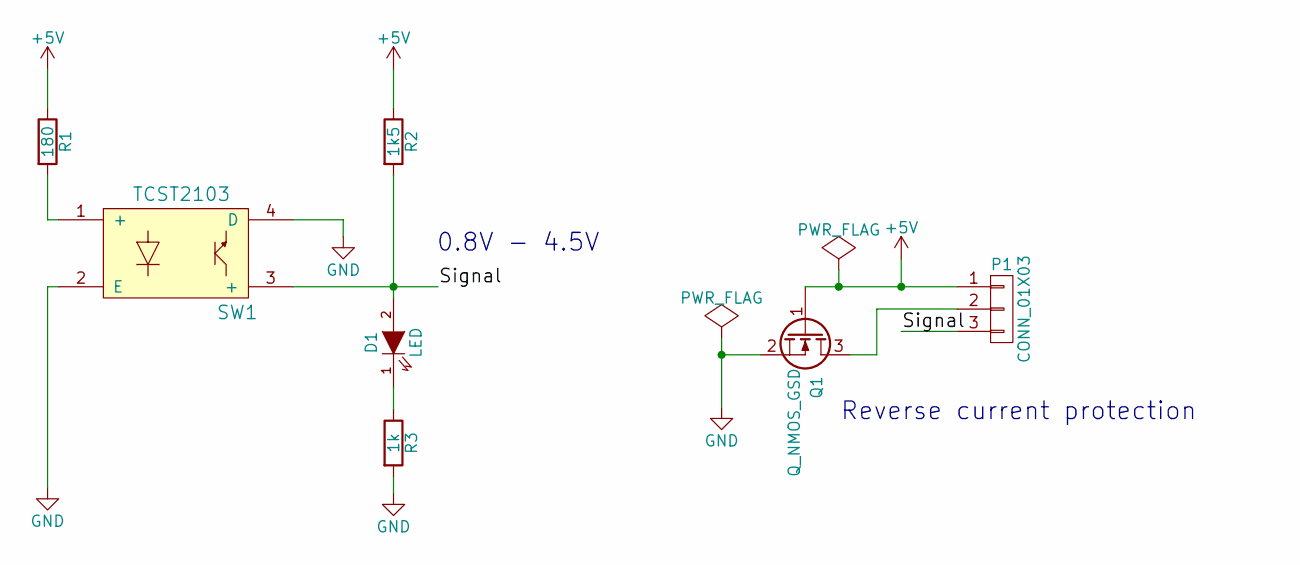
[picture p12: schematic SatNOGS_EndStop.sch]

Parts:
D1: LED; LED-3MM
P1: CONN_01X03; Pin_Header_Angled_1x03
Q1: Q_NMOS_GSD; SOT-23_Handsoldering
R1: 180; R_0805_HandSoldering
R2: 1k5; R_0805_HandSoldering
R3: 1k; R_0805_HandSoldering
SW1: TCST2103

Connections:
+5V: P1.1, Q1.1 (G), R1.1, R2.1
/Signal: D1.2 (A), P1.3, R2.2, SW1.3 (+)
GND: Q1.2 (S), R3.2, SW1.2 (E), SW1.4 (D)
unnamed: D1.1 (K), R3.1
unnamed: P1.2, Q1.3 (D)
unnamed: R1.2, SW1.1 (+)

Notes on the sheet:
Reverse current protection
0.8V - 4.5V

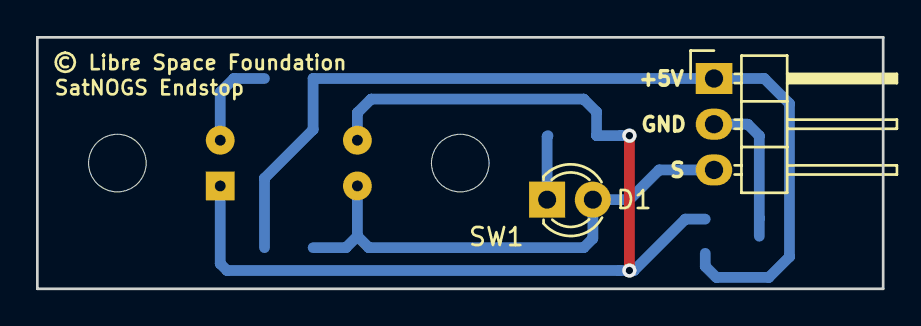
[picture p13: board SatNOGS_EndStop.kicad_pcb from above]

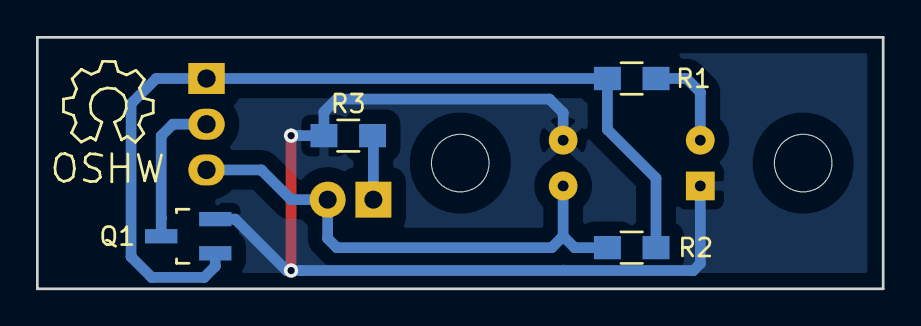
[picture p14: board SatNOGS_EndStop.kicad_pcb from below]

Board: 2 copper layers, 47.0 x 14.0 mm, 8 parts (5 on the bottom side), 6 nets.

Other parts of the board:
SatNOGS Endstop: © Libre Space Foundation; Symbol_OSHW-Logo_SilkScreen

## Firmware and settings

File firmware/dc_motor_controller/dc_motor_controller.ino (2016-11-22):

#include "SoftI2CMaster.h"
#include <Wire.h>
//#include <avr/wdt.h>

/* H-bridge defines */
#define PWM1M1 5
#define PWM2M1 6
#define PWM1M2 9
#define PWM2M2 10
/* Limits for control signal */
#define outMax 120
#define outMin 35
#define Deadband 1
/* Encoder defines */
#define sda_pin 16
#define scl_pin 14
#define as5601_adr 0x36
#define raw_ang_high 0x0c
#define raw_ang_low 0x0d
#define status_reg 0x0b
/* Ratio of worm gear */
#define RATIO 30
/* Maximum Angle for homing scanning */
#define SEEK_MOVE 30
#define MIN_AZ_ANGLE 0
#define MAX_AZ_ANGLE 370
#define MIN_EL_ANGLE 0
#define MAX_EL_ANGLE 110
/* Homing switch */
#define HOME_AZ 4
#define HOME_EL 7
/* Change to LOW according to Home sensor */
#define DEFAULT_HOME_STATE 1
/* Time to disable the motors in millisecond */
#define T_DELAY 1000
/* PIN for Enable or Disable Stepper Motors */
#define EN 8
/* Serial configuration */
#define BufferSize 256
#define BaudRate 19200
#define TX_EN A3
/*Global Variables*/
unsigned long t_DIS = 0; /*time to disable the Motors*/
/* angle offset */
double az_angle_offset = 0;
double el_angle_offset = 0;
/* Encoder */
SoftI2CMaster i2c_soft = SoftI2CMaster(scl_pin, sda_pin, 1);

void setup()
{
  /* H-bridge */
  pinMode(OUTPUT, PWM1M1);
  pinMode(OUTPUT, PWM2M1);
  pinMode(OUTPUT, PWM1M2);
  pinMode(OUTPUT, PWM2M2);
  /* Encoder */
  i2c_soft.begin();
  Wire.begin();
  /* Enable Motors */
  pinMode(EN, OUTPUT);
  digitalWrite(EN, HIGH);
  /* Homing switch */
  pinMode(HOME_AZ, INPUT_PULLUP);
  pinMode(HOME_EL, INPUT_PULLUP);
  /* Serial Communication */
  Serial.begin(BaudRate);
  /* RS485 */
  //Serial1.begin(BaudRate);
  pinMode(TX_EN, OUTPUT);
  digitalWrite(TX_EN, LOW);
  /* WDT */
  //cli();
  //WDTCSR |= (1<<WDCE) | (1<<WDE);
  //WDTCSR = (0<<WDIE) | (1<<WDE) | (0<<WDP3) | (1<<WDP2) | (1<<WDP1) | (0<<WDP0);
  //sei();
  /* Initial Homing */
  //Homing(-MAX_AZ_ANGLE, -MAX_EL_ANGLE, true);
}

void loop()
{
  double *set_point;
  double curr_pos[2];

  /* Read commands from serial */
  set_point = cmd_proc();
  //set_point = cmd_proc_RS485();
  /* Move Motor */
  dc_move(set_point);
  /* Reset WDT */
  //wdt_reset();
  /* Time Check */
  if (t_DIS == 0)
    t_DIS = millis();
  /* Disable Motors */
  get_position(curr_pos);
  if (abs(curr_pos[0]-set_point[0]) < Deadband && abs(curr_pos[1]-set_point[1]) < Deadband && millis()-t_DIS > T_DELAY)
    digitalWrite(EN, LOW);
  /* Enable Motors */
  else
    digitalWrite(EN, HIGH);
}

///* EasyComm 2 Protocol for RS485 */
//double * cmd_proc_RS485()
//{
//  static double set_point[] = {0, 0};
//  /* Serial */
//  static char buffer[BufferSize];
//  char incomingByte;
//  char *Data = buffer;
//  char *rawData;
//  static int BufferCnt = 0;
//  char data[100];
//  double pos[2];
//
//  /* Read from serial */
//  while (Serial1.available() > 0)
//  {
//    incomingByte = Serial1.read();
//    /* New data */
//    if (incomingByte == '\n')
//    {
//      buffer[BufferCnt] = 0;
//      if (buffer[0] == 'A' && buffer[1] == 'Z')
//      {
//        if (buffer[2] == ' ' && buffer[3] == 'E' && buffer[4] == 'L')
//        {
//          get_position(pos);
//          /* Get position */
//          digitalWrite(TX_EN, HIGH);
//          delay(8);
//          Serial1.print("AZ");
//          Serial1.print(pos[0], 1);
//          Serial1.print(" ");
//          Serial1.print("EL");
//          Serial1.println(pos[1], 1);
//          delay(8);
//          digitalWrite(TX_EN, LOW);
//        }
//        else
//        {
//          /* Get the absolute value of angle */
//          rawData = strtok_r(Data, " " , &Data);
//          strncpy(data, rawData + 2, 10);
//          if (isNumber(data))
//          {
//            set_point[0] = atof(data);
//            if (set_point[0] > MAX_AZ_ANGLE)
//              set_point[0] = MAX_AZ_ANGLE;
//            else if (set_point[0] < MIN_AZ_ANGLE)
//              set_point[0] = MIN_AZ_ANGLE;
//          }
//          /* Get the absolute value of angle */
//          rawData = strtok_r(Data, " " , &Data);
//          if (rawData[0] == 'E' && rawData[1] == 'L')
//          {
//            strncpy(data, rawData + 2, 10);
//            if (isNumber(data))
//            {
//              set_point[1] = atof(data);
//              if (set_point[1] > MAX_EL_ANGLE)
//                set_point[1] = MAX_EL_ANGLE;
//              else if (set_point[1] < MIN_EL_ANGLE)
//                set_point[1] = MIN_EL_ANGLE;
//            }
//          }
//        }
//      }
//      /* Stop Moving */
//      else if (buffer[0] == 'S' && buffer[1] == 'A' && buffer[2] == ' ' && buffer[3] == 'S' && buffer[4] == 'E')
//      {
//        get_position(pos);
//        /* Get position */
//        digitalWrite(TX_EN, HIGH);
//        delay(8);
//        Serial1.print("AZ");
//        Serial1.print(pos[0], 1);
//        Serial1.print(" ");
//        Serial1.print("EL");
//        Serial1.println(pos[1], 1);
//        delay(8);
//        digitalWrite(TX_EN, LOW);
//        set_point[0] = pos[0];
//        set_point[1] = pos[1];
//      }
//      /* Reset the rotator */
//      else if (buffer[0] == 'R' && buffer[1] == 'E' && buffer[2] == 'S' && buffer[3] == 'E' && buffer[4] == 'T')
//      {
//        get_position(pos);
//        /* Get position */
//        digitalWrite(TX_EN, HIGH);
//        delay(8);
//        Serial1.print("AZ");
//        Serial1.print(pos[0], 1);
//        Serial1.print(" ");
//        Serial1.print("EL");
//        Serial1.println(pos[1], 1);
//        delay(8);
//        digitalWrite(TX_EN, LOW);
//        /* Move to initial position */
//        Homing(-MAX_AZ_ANGLE, -MAX_EL_ANGLE, false);
//        set_point[0] = 0;
//        set_point[1] = 0;
//      }
//      /* Clear serial buffer */
//      BufferCnt = 0;
//      Serial1.read();
//      /* Reset the disable motor time */
//      t_DIS = 0;
//    }
//    /* Fill the buffer with incoming data */
//    else {
//      buffer[BufferCnt] = incomingByte;
//      BufferCnt++;
//    }
//  }
//  return set_point;
//}

/* Homing Function */
void Homing(double AZangle, double ELangle, bool Init)
{
  int value_Home_AZ = DEFAULT_HOME_STATE;
  int value_Home_EL = DEFAULT_HOME_STATE;
  boolean isHome_AZ = false;
  boolean isHome_EL = false;
  double zero_angle[2];
  double curr_angle[2];
  double set_point[2];

  get_position(zero_angle);
  if (Init == true)
  {
    set_point[0] = zero_angle[0]+SEEK_MOVE;
    set_point[1] = zero_angle[1]+SEEK_MOVE;
  }
  else
  {
    set_point[0] = 10;//zero_angle[0]-MAX_AZ_ANGLE;
    set_point[1] = 10;//zero_angle[1]-MAX_EL_ANGLE;
  }
  while (isHome_AZ == false || isHome_EL == false)
  {
    dc_move(set_point);
    delay(1);
    value_Home_AZ = digitalRead(HOME_AZ);
    delay(1);
    value_Home_EL = digitalRead(HOME_EL);
    /* Change to LOW according to Home sensor */
    if (value_Home_AZ == DEFAULT_HOME_STATE && isHome_AZ == false)
    {
      isHome_AZ = true;
      get_position(curr_angle);
      set_point[0] = 0;
      if (Init)
        az_angle_offset = curr_angle[0];
    }
    if (value_Home_EL == DEFAULT_HOME_STATE && isHome_EL == false)
    {
      isHome_EL = true;
      get_position(curr_angle);
      set_point[1] = 0;
      if (Init)
        el_angle_offset = curr_angle[1];
    }
    get_position(curr_angle);
    if (abs(curr_angle[0] - zero_angle[0]) >= SEEK_MOVE && !isHome_AZ && Init)
      set_point[0] = -MAX_AZ_ANGLE;
    if (abs(curr_angle[1] - zero_angle[1]) >= SEEK_MOVE && !isHome_EL && Init)
      set_point[1] = -MAX_EL_ANGLE;
    if ((abs(curr_angle[0] - zero_angle[0]) >= MAX_AZ_ANGLE && !isHome_AZ) || (abs(curr_angle[1] - zero_angle[1]) >= MAX_EL_ANGLE && !isHome_EL))
    {
      /* set error */
      while(1)
      {
        ;
      }
    }
  }
}

void dc_move(double set_point[])
{
  double u[2];
  double curr_pos[2];
  static double prev_pos[] = {0, 0};
  double error[2];
  double Iterm[2];
  double Pterm[2];
  double Dterm[2];
  double Kp = 200;
  double Ki = 2;
  double Kd = 0;
  double dt = 0.001; // calculate

  get_position(curr_pos);
  error[0] = set_point[0] - curr_pos[0];
  error[1] = set_point[1] - curr_pos[1];

  Pterm[0] = Kp * error[0];
  Pterm[1] = Kp * error[1];

  Iterm[0] += Ki * error[0] * dt;
  Iterm[1] += Ki * error[1] * dt;
  if (Iterm[0] > outMax) Iterm[0] = outMax;
  else if (Iterm[0] < outMin) Iterm[0] = outMin;
  if (Iterm[1] > outMax) Iterm[1] = outMax;
  else if (Iterm[1] < outMin) Iterm[1] = outMin;

  Dterm[0] = Kd * (curr_pos[0] - prev_pos[0]) / dt;
  prev_pos[0] = curr_pos[0];
  Dterm[1] = Kd * (curr_pos[1] - prev_pos[1]) / dt;
  prev_pos[1] = curr_pos[1];

  u[0] = Pterm[0] + Iterm[0] + Dterm[0];
  u[1] = Pterm[1] + Iterm[1] + Dterm[1];

  if (u[0] >= 0)
  {
    if (u[0] > outMax)
      u[0] = outMax;
    analogWrite(PWM1M1, u[0]);
    analogWrite(PWM2M1, 0);
  }
  else
  {
    u[0] = -u[0];
    if ( u[0] > outMax)
      u[0] = outMax;
    analogWrite(PWM1M1, 0);
    analogWrite(PWM2M1, u[0]);
  }

  if (u[1] >= 0)
  {
    if (u[1] > outMax)
      u[1] = outMax;
    analogWrite(PWM1M2, u[1]);
    analogWrite(PWM2M2, 0);
  }
  else
  {
    u[1] = -u[1];
    if ( u[1] > outMax)
      u[1] = outMax;
    analogWrite(PWM1M2, 0);
    analogWrite(PWM2M2, u[1]);
  }
}

/* Read Encoders */
void get_position(double *new_pos)
{
  int low_raw, high_raw, status_val;
  double raw_pos = 0;
  double delta_raw_pos = 0;
  static double raw_prev_pos[] = {0, 0};
  static double real_pos[] = {0, 0};
  static int n[] = {0, 0};

  /* Axis 1*/
  /* Read Raw Angle Low Byte */
  Wire.beginTransmission(as5601_adr);
  Wire.write(raw_ang_low);
  Wire.endTransmission();
  Wire.requestFrom(as5601_adr, 1);
  while(Wire.available() == 0);
  low_raw = Wire.read();
  /* Read Raw Angle High Byte */
  Wire.beginTransmission(as5601_adr);
  Wire.write(raw_ang_high);
  Wire.endTransmission();
  Wire.requestFrom(as5601_adr, 1);
  while(Wire.available() == 0);
  high_raw = Wire.read();
  high_raw = high_raw << 8;
  high_raw = high_raw | low_raw;
  /* Read Status Bits */
  Wire.beginTransmission(as5601_adr);
  Wire.write(status_reg);
  Wire.endTransmission();
  Wire.requestFrom(as5601_adr, 1);
  while(Wire.available() == 0);
  status_val = Wire.read();
  /* Check the status register */
  if ((status_val & 0x20) && !(status_val & 0x10) && !(status_val & 0x08))
  {
    if (high_raw >= 0)
    {
      raw_pos = (double)high_raw*0.0879;
      delta_raw_pos = raw_prev_pos[0] - raw_pos;
      if (delta_raw_pos > 180)
        n[0]++;
      else if (delta_raw_pos < -180)
        n[0]--;
      real_pos[0] = ((raw_pos + 360 * n[0]) / RATIO) - az_angle_offset;
      raw_prev_pos[0] = raw_pos;
    }
    else
      ; /* set error  */
  }
  else
    ; /* set error */

  /* Axis 2 */
  /* Read Raw Angle Low Byte */
  i2c_soft.beginTransmission(as5601_adr);
  i2c_soft.write(raw_ang_low);
  i2c_soft.endTransmission();
  i2c_soft.requestFrom(as5601_adr);
  low_raw = i2c_soft.readLast();
  i2c_soft.endTransmission();
  /* Read Raw Angle High Byte */
  i2c_soft.beginTransmission(as5601_adr);
  i2c_soft.write(raw_ang_high);
  i2c_soft.endTransmission();
  i2c_soft.requestFrom(as5601_adr);
  high_raw = i2c_soft.readLast();
  i2c_soft.endTransmission();
  high_raw = high_raw << 8;
  high_raw = high_raw | low_raw;
  /* Read Status Bits */
  i2c_soft.beginTransmission(as5601_adr);
  i2c_soft.write(status_reg);
  i2c_soft.endTransmission();
  i2c_soft.requestFrom(as5601_adr);
  status_val = i2c_soft.readLast();
  i2c_soft.endTransmission();
  /* Check the status register */
  if ((status_val & 0x20) && !(status_val & 0x10) && !(status_val & 0x08))
  {
    if (high_raw >= 0)
    {
      raw_pos = (double)high_raw*0.0879;
      delta_raw_pos = raw_prev_pos[1] - raw_pos;
      if (delta_raw_pos > 180)
        n[1]++;
      else if (delta_raw_pos < -180)
        n[1]--;
      real_pos[1] = ((raw_pos + 360 * n[1]) / RATIO) - el_angle_offset;
      raw_prev_pos[1] = raw_pos;
    }
    else
      ; /* set error  */
  }
  else
    ; /* set error */

  new_pos[0] = real_pos[0];
  new_pos[1] = real_pos[1];
}

/* EasyComm 2 Protocol */
double * cmd_proc()
{
  static double set_point[] = {0, 0};
  /* Serial */
  char buffer[BufferSize];
  char incomingByte;
  char *Data = buffer;
  char *rawData;
  static int BufferCnt = 0;
  char data[100];
  double pos[2];

  /* Read from serial */
  while (Serial.available() > 0)
  {
    incomingByte = Serial.read();
    /* New data */
    if (incomingByte == '\n')
    {
      buffer[BufferCnt] = 0;
      if (buffer[0] == 'A' && buffer[1] == 'Z')
      {
        if (buffer[2] == ' ' && buffer[3] == 'E' && buffer[4] == 'L')
        {
          get_position(pos);
          /* Get position */
          Serial.print("AZ");
          Serial.print(pos[0], 1);
          Serial.print(" ");
          Serial.print("EL");
          Serial.println(pos[1], 1);
        }
        else
        {
          /* Get the absolute value of angle */
          rawData = strtok_r(Data, " " , &Data);
          strncpy(data, rawData + 2, 10);
          if (isNumber(data))
          {
            set_point[0] = atof(data);
            if (set_point[0] > MAX_AZ_ANGLE)
              set_point[0] = MAX_AZ_ANGLE;
            else if (set_point[0] < MIN_AZ_ANGLE)
              set_point[0] = MIN_AZ_ANGLE;
          }
          /* Get the absolute value of angle */
          rawData = strtok_r(Data, " " , &Data);
          if (rawData[0] == 'E' && rawData[1] == 'L')
          {
            strncpy(data, rawData + 2, 10);
            if (isNumber(data))
            {
              set_point[1] = atof(data);
              if (set_point[1] > MAX_EL_ANGLE)
                set_point[1] = MAX_EL_ANGLE;
              else if (set_point[1] < MIN_EL_ANGLE)
                set_point[1] = MIN_EL_ANGLE;
            }
          }
        }
      }
      /* Stop Moving */
      else if (buffer[0] == 'S' && buffer[1] == 'A' && buffer[2] == ' ' && buffer[3] == 'S' && buffer[4] == 'E')
      {
        get_position(pos);
        /* Get position */
        Serial.print("AZ");
        Serial.print(pos[0], 1);
        Serial.print(" ");
        Serial.print("EL");
        Serial.println(pos[1], 1);
        set_point[0] = pos[0];
        set_point[1] = pos[1];
      }
      /* Reset the rotator */
      else if (buffer[0] == 'R' && buffer[1] == 'E' && buffer[2] == 'S' && buffer[3] == 'E' && buffer[4] == 'T')
      {
        get_position(pos);
        /* Get position */
        Serial.print("AZ");
        Serial.print(pos[0], 1);
        Serial.print(" ");
        Serial.print("EL");
        Serial.println(pos[1], 1);
        /* Move to initial position */
        Homing(-MAX_AZ_ANGLE, -MAX_EL_ANGLE, false);
        set_point[0] = 0;
        set_point[1] = 0;
      }
      BufferCnt = 0;
      /* Reset the disable motor time */
      t_DIS = 0;
    }
    /* Fill the buffer with incoming data */
    else {
      buffer[BufferCnt] = incomingByte;
      BufferCnt++;
    }
  }
  return set_point;
}

/* check if is argument in number */
boolean isNumber(char *input)
{
  for (int i = 0; input[i] != '\0'; i++)
  {
    if (isalpha(input[i]))
      return false;
  }
  return true;
}

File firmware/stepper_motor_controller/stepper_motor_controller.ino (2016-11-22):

#include <string.h>
#include <stdlib.h>
#include <math.h>
#include <AccelStepper.h>

#define DIR_AZ 6 /*PIN for Azimuth Direction*/
#define STEP_AZ 5 /*PIN for Azimuth Steps*/
#define DIR_EL 10 /*PIN for Elevation Direction*/
#define STEP_EL 9 /*PIN for Elevation Steps*/

#define EN 8 /*PIN for Enable or Disable Stepper Motors*/

#define SPR 200 /*Step Per Revolution*/
#define RATIO 54 /*Gear ratio*/
#define T_DELAY 60000 /*Time to disable the motors in millisecond*/

#define HOME_AZ 4 /*Homing switch for Azimuth*/
#define HOME_EL 7 /*Homing switch for Elevation*/

#define MAX_AZ_ANGLE 365 /*Maximum Angle of Azimuth for homing scanning*/
#define MAX_EL_ANGLE 365 /*Maximum Angle of Elevation for homing scanning*/

#define MAX_SPEED 300
#define MAX_ACCELERATION 100

#define MIN_PULSE_WIDTH 20 /*in microsecond*/

#define DEFAULT_HOME_STATE HIGH /*Change to LOW according to Home sensor*/

#define HOME_DELAY 6000 /*Time for homing Decceleration in millisecond*/

#define BufferSize 256
#define BaudRate 19200

/*Global Variables*/
unsigned long t_DIS = 0; /*time to disable the Motors*/
/*Define a stepper and the pins it will use*/
AccelStepper AZstepper(1, STEP_AZ, DIR_AZ);
AccelStepper ELstepper(1, STEP_EL, DIR_EL);

void setup()
{  
  /*Change these to suit your stepper if you want*/
  AZstepper.setMaxSpeed(MAX_SPEED);
  AZstepper.setAcceleration(MAX_ACCELERATION);
  /*Change these to suit your stepper if you want*/
  ELstepper.setMaxSpeed(MAX_SPEED);
  ELstepper.setAcceleration(MAX_ACCELERATION);
  /*Set minimum pulse width*/
  AZstepper.setMinPulseWidth(MIN_PULSE_WIDTH);
  ELstepper.setMinPulseWidth(MIN_PULSE_WIDTH);
  /*Enable Motors*/
  pinMode(EN, OUTPUT);
  digitalWrite(EN, LOW);
  /*Homing switch*/
  pinMode(HOME_AZ, INPUT_PULLUP);
  pinMode(HOME_EL, INPUT_PULLUP);
  /*Serial Communication*/
  Serial.begin(BaudRate);
  /*Initial Homing*/
  Homing(deg2step(-MAX_AZ_ANGLE), deg2step(-MAX_EL_ANGLE));
}

void loop()
{ 
  /*Define the steps*/
  static int AZstep = 0;
  static int ELstep = 0;
  /*Time Check*/
  if (t_DIS == 0)
    t_DIS = millis();

  /*Disable Motors*/
  if (AZstep == AZstepper.currentPosition() && ELstep == ELstepper.currentPosition() && millis()-t_DIS > T_DELAY)
    digitalWrite(EN, HIGH);
  /*Enable Motors*/
  else
    digitalWrite(EN, LOW);
    
  /*Read the steps from serial*/
  cmd_proc(AZstep, ELstep);
  /*Move the Azimuth & Elevation Motor*/
  stepper_move(AZstep, ELstep);
}

/*Homing Function*/
void Homing(int AZsteps, int ELsteps)
{
  int value_Home_AZ = DEFAULT_HOME_STATE;
  int value_Home_EL = DEFAULT_HOME_STATE;
  boolean isHome_AZ = false;
  boolean isHome_EL = false;
  
  AZstepper.moveTo(AZsteps);
  ELstepper.moveTo(ELsteps);
  
  while(isHome_AZ == false || isHome_EL == false)
  {
    value_Home_AZ = digitalRead(HOME_AZ);
    value_Home_EL = digitalRead(HOME_EL);
    /*Change to LOW according to Home sensor*/
    if (value_Home_AZ == DEFAULT_HOME_STATE)
    {
      AZstepper.moveTo(AZstepper.currentPosition());
      isHome_AZ = true;
    }   
    /*Change to LOW according to Home sensor*/
    if (value_Home_EL == DEFAULT_HOME_STATE)
    {
      ELstepper.moveTo(ELstepper.currentPosition());
      isHome_EL = true;
    }
    if (AZstepper.distanceToGo() == 0 && !isHome_AZ)
    {
      error(0);
      break;
    }
    if (ELstepper.distanceToGo() == 0 && !isHome_EL)
    {
      error(1);
      break;
    }
    AZstepper.run();
    ELstepper.run();
  }
  /*Delay to Deccelerate*/
  long time = millis();  
  while(millis() - time < HOME_DELAY)
  {  
    AZstepper.run();
    ELstepper.run();
  }
  /*Reset the steps*/
  AZstepper.setCurrentPosition(0);
  ELstepper.setCurrentPosition(0); 
}
 
/*EasyComm 2 Protocol & Calculate the steps*/
void cmd_proc(int &stepAz, int &stepEl)
{
  /*Serial*/
  char buffer[BufferSize];
  char incomingByte;
  char *Data = buffer;
  char *rawData;
  static int BufferCnt = 0;
  char data[100];
  
  double angleAz, angleEl;
  
  /*Read from serial*/
  while (Serial.available() > 0)
  {
    incomingByte = Serial.read();
    /* XXX: Get position using custom and test code */
    if (incomingByte == '!')
    {
      /*Get position*/
      Serial.print("TM");
      Serial.print(1);
      Serial.print(" ");
      Serial.print("AZ");
      Serial.print(10*step2deg(AZstepper.currentPosition()), 1);
      Serial.print(" ");
      Serial.print("EL");
      Serial.println(10*step2deg(ELstepper.currentPosition()), 1);
    }
    /*new data*/
    else if (incomingByte == '\n')
    {
      buffer[BufferCnt] = 0;
      if (buffer[0] == 'A' && buffer[1] == 'Z')
      {
        if (buffer[2] == ' ' && buffer[3] == 'E' && buffer[4] == 'L')
        {
          /*Get position*/
          Serial.print("AZ");
          Serial.print(step2deg(AZstepper.currentPosition()), 1);
          Serial.print(" ");
          Serial.print("EL");
          Serial.print(step2deg(ELstepper.currentPosition()), 1);
          Serial.println(" ");
        }
        else
        {
          /*Get the absolute value of angle*/
          rawData = strtok_r(Data, " " , &Data);
          strncpy(data, rawData+2, 10);
          if (isNumber(data))
          {
            angleAz = atof(data);
            /*Calculate the steps*/
            stepAz = deg2step(angleAz);
          }
          /*Get the absolute value of angle*/
          rawData = strtok_r(Data, " " , &Data);
          if (rawData[0] == 'E' && rawData[1] == 'L')
          {
            strncpy(data, rawData+2, 10);
            if (isNumber(data))
            {
              angleEl = atof(data);
              /*Calculate the steps*/
              stepEl = deg2step(angleEl);
            }
          }
        }
      }
      /*Stop Moving*/
      else if (buffer[0] == 'S' && buffer[1] == 'A' && buffer[2] == ' ' && buffer[3] == 'S' && buffer[4] == 'E')
      {
        /*Get position*/
        Serial.print("AZ");
        Serial.print(step2deg(AZstepper.currentPosition()), 1);
        Serial.print(" ");
        Serial.print("EL");
        Serial.println(step2deg(ELstepper.currentPosition()), 1);
        stepAz = AZstepper.currentPosition();
        stepEl = ELstepper.currentPosition();
      }
      /*Reset the rotator*/
      else if (buffer[0] == 'R' && buffer[1] == 'E' && buffer[2] == 'S' && buffer[3] == 'E' && buffer[4] == 'T')
      {
        /*Get position*/
        Serial.print("AZ");
        Serial.print(step2deg(AZstepper.currentPosition()), 1);
        Serial.print(" ");
        Serial.print("EL");
        Serial.println(step2deg(ELstepper.currentPosition()), 1);
        /*Move the steppers to initial position*/
        Homing(deg2step(-MAX_AZ_ANGLE), deg2step(-MAX_EL_ANGLE));
        /*Zero the steps*/
        stepAz = 0;
        stepEl = 0;
      }      
      BufferCnt = 0;
      /*Reset the disable motor time*/
      t_DIS = 0;
    }
    /*Fill the buffer with incoming data*/
    else {
      buffer[BufferCnt] = incomingByte;
      BufferCnt++;
    }
  }
}
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
